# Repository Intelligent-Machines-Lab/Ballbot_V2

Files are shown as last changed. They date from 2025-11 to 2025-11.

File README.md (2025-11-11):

# Ballbot_LMI_V2

**Author:** Leandro Ventricci  
**Advisor:** Prof. Dr. Cairo Lúcio Nascimento Júnior

This repository contains the source code, STL files, and experimental results developed during research on the Ballbot platform as part of the Master of Science program in Systems and Control at the Instituto Tecnológico de Aeronáutica (ITA). The work represents a second iteration and expansion of the initial Ballbot project proposed in the master’s thesis available at [Ballbot_LMI_V1](https://github.com/pedrophj/ballbot_LMI/tree/main).

## Repository Structure

| Directory | Description |
|---|---|
| [**`/Experimental Results/Data Bags`**](./Experimental%20Results/Data%20Bags/) | Provides the ROS bag files acquired during the experiments, which contain the recorded ROS topic data used for analysis. |
| [**`/Experimental Results/Videos`**](./Experimental%20Results/Videos/) | Provides video recordings of the experimental results obtained with the Ballbot prototype. The videos are also available online at [Google Drive](https://drive.google.com/drive/folders/1ocQBuRk292TQQt81lqkflchQvDIo9T61?usp=sharing). |
| [**`/Microcontroller`**](/Microcontroller/src) | Provides the PlatformIO project containing the ESP32 firmware. |
| [**`/STL`**](/STL/) | Provides the STL files for the mechanical structure of the Ballbot for 3D printing. |
| [**`/Simulations/2D`**](/Simulations/2D) | Provides the MATLAB simulations for the X–Z and X–Y planar models, used for control design and validation. |
| [**`/Simulations/3D`**](/Simulations/3D) | Provides the CoppeliaSim files of the environment developed to validate the 2D model using a full 3D representation of the Ballbot. |

## MATLAB Simulations

The MATLAB simulation files for the Ballbot’s dynamic modeling and control are available in the [**`/Simulations/2D`**](/Simulations/2D) directory.  
These simulations cover both the X–Z and X–Y planar models, developed using **MATLAB version 2023b**.

## 3D Simulation Environment

The 3D simulation files are available in the [**`/Simulations/3D`**](/Simulations/3D) directory. The environment was developed using **CoppeliaSim Edu version 4.10**.

## Bill of Materials

The tables below list the electronic and structural components required to assemble and operate the Ballbot prototype, including specifications, quantities, and supply sources when applicable.

### Electronics

| Component | Model / Specification | Quantity |
|---|---|:---:|
| Microcontroller | ESP32-WROOM-32 | 1 |
| Microcomputer | Raspberry Pi 4 Model B (4GB) | 1 |
| Stepper Motors | NEMA 17 (17HS4401) | 3 |
| Motor Drivers | DRV8825 | 3 |
| IMU | Witmotion WT901C | 1 |
| LiDAR Sensor | RPLIDAR A2M8 | 1 |

### Structure Parts

| Part | Quantity |
|---|:---:|
| Layer 0 | 1 |
| Layer 1 | 1 |
| Layer 2 | 1 |
| Layer 3 | 1 |
| Motor Support - Layer 0 Side | 3 |
| Motor Support - Motor Side | 3 |
| Support - Layer 1 | 3 |
| Support - Layer 2 | 3 |
| Support - Layer 3 | 3 |
| Support for Electronics - Layer 1 | 1 |
| Battery Support - BMS | 1 |
| Battery Support - Connectors | 1 |
| Wheel Assembly | 3 |

### Wheel Assembly

| Part | Quantity | Notes |
|---|:---:|:---:|
| Fork | 6 | - |
| Roller - Small | 6 | - |
| Roller - Big | 6 | - |
| Motor Coupling | 1 | - |
| Motor Coupling Cap | 1 | - |
| MR52ZZ Spherical Bearing | 24 | Available at: [Aliexpress](https://pt.aliexpress.com/item/32492575669.html) |

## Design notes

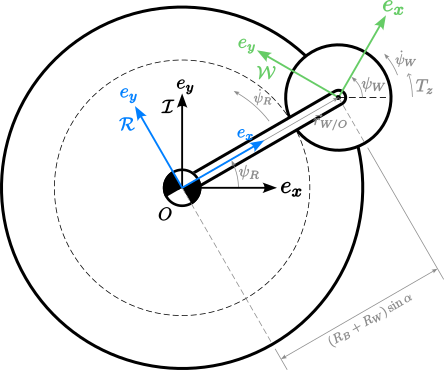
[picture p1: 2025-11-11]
Simulations/2D/XY/XY.png

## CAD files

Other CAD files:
STL/Body Structure/Support for Electronics - Layer 1.STL
STL/Wheel/Roller - Big.STL
STL/Body Structure/Motor Support - Layer 0 Side.STL
STL/Wheel/Roller - Small.STL
STL/Body Structure/Support - Layer 3.STL
STL/Wheel/Motor Coupling Cap.STL
STL/Body Structure/Layer 0.STL
STL/Wheel/Motor Coupling.STL
STL/Body Structure/Layer 2.STL
STL/Wheel/Fork.STL
STL/Body Structure/Support - Layer 1.STL
STL/Body Structure/Battery Support - BMS.STL
STL/Body Structure/Layer 3.STL
STL/Body Structure/Battery Support - Connector.STL
STL/Body Structure/Motor Support - Motor Side.STL
STL/Body Structure/Support - Layer 2.STL
STL/Body Structure/Layer 1.STL

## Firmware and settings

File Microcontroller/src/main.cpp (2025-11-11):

#include "wit_c_sdk.h"
#include "reg.h"
#include <BasicLinearAlgebra.h>
#include <Arduino.h>
#include <ArduinoOTA.h>
#include <AccelStepper.h>
#include <PID_v1_bc.h>
#include <WiFi.h>
   
#define LED_OB        2
#define RX            16
#define TX            17
#define ACC_UPDATE		0x01
#define GYRO_UPDATE		0x02
#define ANGLE_UPDATE	0x04
#define MAG_UPDATE		0x08
#define READ_UPDATE		0x80
#define g             9.81

#define MS1   33
#define MS2   14
#define MS3   32

#define MOTOR_1_STEP 12
#define MOTOR_1_DIR 13

#define MOTOR_2_STEP 19
#define MOTOR_2_DIR 18

#define MOTOR_3_STEP 25
#define MOTOR_3_DIR 26

using namespace BLA;

Matrix<3> gravity_world = {0, 0, g};
Matrix<4> pos_world, pos_robot;
Matrix<3> vel_world_out, vel_robot_out;   // Velocity data comming from sensors other than the IMU (not directly connected to the ESP32)
Matrix<3> vel_world_odom, vel_robot_odom; // Velocity data from wheels velocity
Matrix<4> vel_world, vel_world_imu, vel_robot, vel_robot_imu;
Matrix<4, 4> R_yaw;

struct FilterState {
  float filteredValue;
  bool firstRun;
}; 
FilterState gyroXFilter, gyroYFilter, gyroZFilter, 
            accXFilter, accYFilter, accZFilter,
            txFilter, tyFilter;

float lowPassFilter(float rawValue, float alpha, FilterState* state);
float alphaAccel = 1.0, alphaGyro = 0.75, alphaTorque = 1.0;

bool debug = false;
int calibDuration = 0;
int loopCount = 0, outerLoopCount = 0, integralXCount = 0, integralYCount = 0;

unsigned long timeStart;
int status = 0;

float controlRate = 200;                    // Loop Frequency in Hz
float sampleTime = 1/controlRate;           // Loop Period in s
float sat, satAngle, W1 = 0.0, W2 = 0.0, W3 = 0.0, wx = 0.0, wy = 0.0, wz = 0.0;
double satXY = 5*2*PI;
int controller = 0;

int stepRes = 32;
int stepsPerRev = 200*stepRes;

float accX_world = 0.0, accY_world = 0.0, accZ_world = 0.0, accX_robot = 0.0, accY_robot = 0.0, accZ_robot = 0.0;
float posX_world = 0.0, posY_world = 0.0, posX_world_out = 0.0, posY_world_out = 0.0, posX_world_imu = 0.0, posY_world_imu = 0.0;
float velX_world = 0.0, velY_world = 0.0;
float velX_world_imu = 0.0, velY_world_imu = 0.0;
float velX_robot_out = 0.0, velY_robot_out = 0.0, velX_world_out = 0.0, velY_world_out = 0.0;
float posXRefWorld = 0.0, posYRefWorld = 0.0, velXRefWorld = 0.0, velYRefWorld = 0.0;
float integralErroPosX = 0.0, integralErroPosY = 0.0, erroPosXAnt = 0.0, erroPosYAnt = 0.0;
float satErroPos = 0.30, satErroVel = 1.0;
float pitchMax = 1.0, rollMax = 1.0;

bool posXUpdate, posYUpdate;

struct Quaternion {
  float w, x, y, z;
};

Quaternion conjugate(Quaternion q);
Quaternion multiply(Quaternion q_1, Quaternion q_2);
Quaternion yawToQuaternion(float yaw);

float quaternionToYaw(Quaternion q);

// ------------------------------ Define the State and Controller parameters ------------------------------
struct State {
  double posX = 0.0;      // x position   [m]
  double velX = 0.0;      // x velocity   [m/s]
  double theta = 0.0;     // pitch angle  [rad]
  double q = 0.0;         // pitch rate   [rad/s]
  double posY = 0.0;      // y position   [m]
  double velY = 0.0;      // y velocity   [m/s]
  double phi = 0.0;       // roll angle   [rad]
  double p = 0.0;         // roll rate    [rad/s]
  double psi = 0.0;       // yaw angle    [rad]
  double r = 0.0;         // yaw rate     [rad/s]
};
State x, xRef;

double yawError = 0, yawErrorRef = 0;
double refTheta = 0.0, refPhi = 0.0;
double rollOffset = 0.0, pitchOffset = 0.0;
double tx = 0.0, ty = 0.0, tz = 0.0, rateTx = 0.0, rateTy = 0.0, rateTz = 0.0;
double k1 = -35.0/100.0, k2 = -110.0/100.0, k3 = 280.0/100.0, k4 = 40.0/100.0;      // Tune these values as necessary
double kp = 165.0/100.0, ki = 1.0/100.0, kd = 13.0/100.0;                         
double arKp = 0.0, arKi = 0.0, arKd = 0.0;
double posKp = 5.0/100.0, posKi = 0.0, posKd = 0.05/100.0;                      
double velKp = 10.0/100.0, velKi = 0.0, velKd = 0.5/100.0;                      
double kpYaw = 4.0/100.0, kiYaw = 0.0, kdYaw = 1.25/100;
// ---------------------------------------------------------------------------------------

// ------------------- IMU Functions and Variables -------------------
static volatile char s_cDataUpdate = 0, s_cCmd = 0xff; 
static void AutoScanSensor(void);
static void SensorUartSend(uint8_t *p_data, uint32_t uiSize);
static void SensorDataUpdata(uint32_t uiReg, uint32_t uiRegNum);
static void Delayms(uint16_t ucMs);
float fAcc[3], fGyro[3], fAngle[3];
// -------------------------------------------------------------------

//  ------------ Define PID controllers for roll and pitch ------------
PID rollPID(&x.phi, &tx, &xRef.phi, kp, ki, kd, DIRECT);
PID pitchPID(&x.theta, &ty, &xRef.theta, kp, ki, kd, DIRECT);
// PID yawPID(&x.psi, &tz, &xRef.psi, kpYaw, kiYaw, kdYaw, DIRECT);
PID yawPID(&yawError, &tz, &yawErrorRef, kpYaw, kiYaw, kdYaw, REVERSE);

PID rollRatePID(&x.p, &rateTx, &xRef.p, arKp, arKi, arKd, DIRECT);
PID pitchRatePID(&x.q, &rateTy, &xRef.q, arKp, arKi, arKd, DIRECT);
// PID yawRatePID();

PID posXPID(&x.posX, &xRef.velX, &xRef.posX, posKp, posKi, posKd, DIRECT);    // ty acts on X position -> Visualize 2D Model 
PID posYPID(&x.posY, &xRef.velY, &xRef.posY, posKp, posKi, posKd, DIRECT);    // tx acts on Y position 

PID velXPID(&x.velX, &refTheta, &xRef.velX, velKp, velKi, velKd, DIRECT);
PID velYPID(&x.velY, &refPhi, &xRef.velY, velKp, velKi, velKd, REVERSE);
// --------------------------------------------------------------------

// ------------------- Step Motor Objects -------------------
AccelStepper stepper1(1, MOTOR_1_STEP, MOTOR_1_DIR);
AccelStepper stepper2(1, MOTOR_2_STEP, MOTOR_2_DIR);
AccelStepper stepper3(1, MOTOR_3_STEP, MOTOR_3_DIR);
// ----------------------------------------------------------

// -------------- ESP32 to Raspberry Coms --------------
const uint8_t START_BYTE = 0xAA;
const uint8_t END_BYTE = 0xFF;

struct DataPacket {
    float fAngle[3];    // Angles of Attitude (Roll Pitch Yaw)
    float fGyro[3];     // Angular Velocity -> Robot Frame
    float fAcc[3];      // Linear Acceleration -> Robot "Leveled" Frame
    float vel[2];       // Linear Velocity -> Robot "Leveled" Frame
    float pos[2];       // Position -> World Frame
    float W[3];         // Angular Velocities of the planar wheels (2D Model Wheel)
};

DataPacket data;
void sendData(DataPacket data);
// -----------------------------------------------------

TaskHandle_t C0;
void loop2(void *pvParameters);
double saturate(double V, double sat);

const char* ssid = "$$$$"; // Replace with your SSID for the wifi network for OTA (Over the Air) code upload, if needed
const char* password = "$$$$"; // Replace with the password for the wifi network
bool wifiEnabled;
unsigned long wifiStartTime = 0;
const unsigned long wifiTimeout = 300000; // Wifi Timeout in milliseconds (5 minutes)

void disableWiFi();
void enableWiFiAndOTA();
void blinkLED(int times);
void velocityConversion();
Matrix<3, 3> rotationMatrix(const int& axis, const float& angle);
Matrix<4, 4> transformMatrix(const float& angle, Matrix<4> position);
Matrix<3, 3> robotToWorldRotation(const Matrix<3>& angles);

// ------------------ LQR Controller ------------------
class LQR {
  private:
    double k1, k2, k3, k4;

  public:
    // Constructor to initialize LQR gains
    LQR(double k1, double k2, double k3, double k4) {
      this->k1 = k1;
      this->k2 = k2;
      this->k3 = k3;
      this->k4 = k4;
    }

    void setGains(double k1, double k2, double k3, double k4) {
      this->k1 = k1;
      this->k2 = k2;
      this->k3 = k3;
      this->k4 = k4;
    }

    // Update function to calculate control inputs
    // State Vector x -> [x, x_dot, theta, theta_dot, y, y_dot, phi, phi_dot]
    void update(State xRef, State x, double &tx, double &ty) {
      // Calculate the error for each variable
      double erroPosX = xRef.posX - x.posX;
      double erroVelX = xRef.velX - x.velX;
      double erroTheta = xRef.theta - x.theta;
      double erroq = xRef.q - x.q;

      double erroPosY = xRef.posY - x.posY;
      double erroVelY = xRef.velY - x.velY;
      double erroPhi = xRef.phi - x.phi;
      double errop = xRef.p - x.p;

      // Anti-windup for X and Y position controllers
      // When the counter is active (greater than 0), the corresponding integrator value 
      // is gradually reduced at each iteration to prevent saturation.
      if ((erroPosXAnt < 0 && erroPosX > 0) || (erroPosXAnt > 0 && erroPosX < 0))
      {
          integralXCount = 200;
      }

      if ((erroPosYAnt < 0 && erroPosY > 0) || (erroPosYAnt > 0 && erroPosY < 0))
      {
          integralYCount = 200;
      }
      
      if (integralXCount > 0)
      {
          integralXCount--;
          integralErroPosX *= 0.98;
      }

      if (integralYCount > 0)
      {
          integralYCount--;
          integralErroPosY *= 0.98;
      }

      erroPosXAnt = erroPosX;
      erroPosYAnt = erroPosY;

      // This tries to compensate for the mass unbalance on the x-z plane (we have only one motor at the front of the robot and two at the rear)
      if (erroPosX > satErroPos*1.2) erroPosX = satErroPos*1.2;
      if (erroPosX < -satErroPos) erroPosX = -satErroPos;
      // erroPosX = saturate(erroPosX, satErroPos);
      erroPosY = saturate(erroPosY, satErroPos*1.25);

      integralErroPosX += erroPosX*sampleTime;
      integralErroPosY += erroPosY*sampleTime;

      integralErroPosX = saturate(integralErroPosX, 1.25*satErroPos);
      integralErroPosY = saturate(integralErroPosY, 1.25*satErroPos);
      
      float absErroX = fabs(erroPosX);
      float absErroY = fabs(erroPosY);

      tx = -(integralErroPosY*ki) + (erroPosY * k1) + (erroVelY * k2) + (erroPhi * k3) + (errop * k4);    
      ty = (integralErroPosX*ki) - (erroPosX * k1) - (erroVelX * k2) + (erroTheta * k3) + (erroq * k4);
    }
};

LQR lqrController(k1, k2, k3, k4);
// ----------------------------------------------------

#pragma pack(push, 1)
struct CommandPacket {
    uint8_t start_byte;
    uint8_t cmd_type;
    float cmd_value;
    uint8_t end_byte;
};
#pragma pack(pop)

enum CommandType {
    CMD_CONTROLLER_SELECT = 0,
    CMD_KP,
    CMD_KI,
    CMD_KD,
    CMD_KP_ANGLE_RATE,
    CMD_KI_ANGLE_RATE,
    CMD_KD_ANGLE_RATE,
    CMD_KP_POS,
    CMD_KI_POS,
    CMD_KD_POS,
    CMD_KP_VEL,
    CMD_KI_VEL,
    CMD_KD_VEL,
    CMD_K1,
    CMD_K2,
    CMD_K3,
    CMD_K4,
    CMD_KP_YAW,
    CMD_KI_YAW,
    CMD_KD_YAW,
    CMD_SATURATION,
    CMD_POS_X,
    CMD_POS_Y,
    CMD_VEL_X,
    CMD_VEL_Y,
    CMD_YAW,
    CMD_POS_X_SETPOINT,
    CMD_POS_Y_SETPOINT,
    CMD_VEL_X_SETPOINT,
    CMD_VEL_Y_SETPOINT,
    CMD_ROLL_SETPOINT,
    CMD_PITCH_SETPOINT,
    CMD_YAW_SETPOINT,
    CMD_ACCEL_FILTER,
    CMD_GYRO_FILTER,
    CMD_TORQUE_FILTER,
    CMD_SAT_ERRO_POS,
    CMD_SAT_ERRO_VEL,
    CMD_ROLL_MAX,
    CMD_PITCH_MAX,
    CMD_WIFI_MODE,
    CMD_ACCEL_CALIB,
    CMD_DEBUG,
    CMD_MICRO_STEP,
    NUM_COMMANDS
};
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
void loop() {
  for(;;) {
    /*
      Motor angular velocity unit is -> Wn [rad/s]
      setSpeed input is [steps/s]
      We must convert from [rad/s] to [steps/s]
      As we are using micro-stepping, one revolution (2pi) has 6400 steps. (e.g. microstepping set to 32, then 200*32)
      We have to multiply V by 6400/2pi [steps/rad].
      1/(2pi) = 0.15915
    */   
    if (controller == -1) {
      stepper1.setSpeed(stepsPerRev * 0.15915 * k1);
      stepper2.setSpeed(stepsPerRev * 0.15915 * k2);
      stepper3.setSpeed(stepsPerRev * 0.15915 * k3);
    }

    else {
      stepper1.setSpeed(stepsPerRev * 0.15915 * W1);
      stepper2.setSpeed(stepsPerRev * 0.15915 * W2);
      stepper3.setSpeed(stepsPerRev * 0.15915 * W3);
    }

    // Run motors
    stepper1.runSpeed();
    stepper2.runSpeed();
    stepper3.runSpeed();
  }
}

void loop2( void *pvParameters ) {
  for(;;) {     
    timeStart = micros(); 

    cmdHandler.processSerial();

    // Handle OTA updates if Wi-Fi is enabled
    if (wifiEnabled) {
      ArduinoOTA.handle();

      // Automatically disable Wi-Fi after a timeout
      if (millis() - wifiStartTime > wifiTimeout) {
        disableWiFi();
      }
    }

    while (Serial1.available())
    {
      WitSerialDataIn(Serial1.read());
    }

    if(s_cDataUpdate)
    {
      for(int i = 0; i < 3; i++)
      {
        fAcc[i] = sReg[AX+i] / 32768.0f * 16.0f;
        fGyro[i] = sReg[GX+i] / 32768.0f * 2000.0f;
        fAngle[i] = sReg[Roll+i] / 32768.0f * 180.0f;
      }
      
      if(s_cDataUpdate & ACC_UPDATE); s_cDataUpdate &= ~ACC_UPDATE;		
      if(s_cDataUpdate & GYRO_UPDATE); s_cDataUpdate &= ~GYRO_UPDATE;
      if(s_cDataUpdate & ANGLE_UPDATE); s_cDataUpdate &= ~ANGLE_UPDATE;			
      if(s_cDataUpdate & MAG_UPDATE); s_cDataUpdate &= ~MAG_UPDATE;
      
      s_cDataUpdate = 0;
    }

    x.phi = fAngle[0]*DEG_TO_RAD;                             // [rad]
    x.theta = fAngle[1]*DEG_TO_RAD;                           // [rad]
    // x.psi = fAngle[2]*DEG_TO_RAD;                          // [rad] Yaw info is comming from Outside 
    
    x.p = fGyro[0]*DEG_TO_RAD;                                // [rad/s]
    x.q = fGyro[1]*DEG_TO_RAD;                                // [rad/s]
    x.r = fGyro[2]*DEG_TO_RAD;                                // [rad/s]
   
    x.p = lowPassFilter(x.p, alphaGyro, &gyroXFilter);
    x.q = lowPassFilter(x.q, alphaGyro, &gyroYFilter);
    x.r = lowPassFilter(x.r, alphaGyro, &gyroZFilter);

    Matrix<3> angles = {(float)x.phi, (float)x.theta, (float)x.psi};

    // We are transforming the Robot's acceleration from body frame to inertial frame
    Matrix<3> acc_robot = {(float)(fAcc[0]*g), (float)(fAcc[1]*g), (float)(fAcc[2]*g)};  // [m/s^2]
    Matrix<3, 3> R_robot_to_world = robotToWorldRotation(angles);
    Matrix<3> acc_world = (R_robot_to_world*acc_robot) - gravity_world;

    accX_world = lowPassFilter(acc_world(0), alphaAccel, &accXFilter);
    accY_world = lowPassFilter(acc_world(1), alphaAccel, &accYFilter);
    accZ_world = lowPassFilter(acc_world(2), alphaAccel, &accZFilter);
    
    vel_robot_odom = {float (-wy*0.07/2), float (wx*0.07/2), 0};
    vel_world_odom = robotToWorldRotation(Matrix<3> {0, 0, (float) x.psi})*vel_robot_odom;

    velX_world_imu = velX_world + accX_world*sampleTime;
    velY_world_imu = velY_world + accY_world*sampleTime;
    vel_world_imu = {velX_world_imu, velY_world_imu, 0, 0};

    velX_world = 0.004*vel_world_odom(0) + 0.996*velX_world_imu;
    velY_world = 0.004*vel_world_odom(1) + 0.996*velY_world_imu;

    vel_world = {velX_world, velY_world, 0, 0};
    vel_robot = R_yaw*vel_world;
    
    x.velX = vel_robot(0); x.velY = vel_robot(1);

    posX_world_imu = posX_world + velX_world_imu*sampleTime;
    posY_world_imu = posY_world + velY_world_imu*sampleTime;

    posX_world = 0.99*posX_world_out + 0.01*posX_world_imu; 
    posY_world = 0.99*posY_world_out + 0.01*posY_world_imu;
    
    pos_world = {posX_world, posY_world, 0, 1};

    // Transforming Acceleration, Position and Velocity to the "Leveled" robot's frame, 
    // which is a frame fixed to the Robot's body and that has its X-Y plane aligned to the Inertial frame X-Y plane.
    // Note that for Position, we're also translating it to the robot's frame, which means the position should be 0 at any time, 
    // as we're measuring the robot's position related to it's own frame of reference that has it's origint at the robot's C.G
    R_yaw = transformMatrix(x.psi, pos_world);    

    pos_robot = R_yaw*pos_world;
    x.posX = pos_robot(0); x.posY = pos_robot(1);

    Matrix<4> acc_robot_leveled = R_yaw * Matrix<4> {acc_world(0), acc_world(1), acc_world(2), 0};
    accX_robot = acc_robot_leveled(0); accY_robot = acc_robot_leveled(1); accZ_robot = acc_robot_leveled(2); 

    Matrix<4> pos_ref_world = {posXRefWorld, posYRefWorld, 0, 1};
    Matrix<4> pos_ref_robot = R_yaw * pos_ref_world;
    xRef.posX = pos_ref_robot(0); xRef.posY = pos_ref_robot(1);    

    Quaternion qSP = yawToQuaternion(xRef.psi);
    Quaternion qCur = yawToQuaternion(x.psi);
    Quaternion qDelta = multiply(qSP, conjugate(qCur));

    yawError = quaternionToYaw(qDelta);
    if ((yawError*RAD_TO_DEG) > 15){
      yawError = 15*DEG_TO_RAD;
    }

    if ((yawError*RAD_TO_DEG) < -15){
      yawError = -15*DEG_TO_RAD;
    }
    
    if (controller == 0)
    {
      // Roll Pitch Yaw
      rollPID.SetSampleTime((int)(sampleTime*1000));      // Input is [ms], converting from [s] to [ms]
      pitchPID.SetSampleTime((int)(sampleTime*1000));     
      yawPID.SetSampleTime((int)(sampleTime*1000));

      rollRatePID.SetSampleTime((int)(sampleTime*100));
      pitchRatePID.SetSampleTime((int)(sampleTime*100));

      xRef.phi = rollOffset;
      xRef.theta = pitchOffset;

      rollPID.Compute();
      pitchPID.Compute();
      yawPID.Compute();

      rollRatePID.Compute();
      pitchRatePID.Compute();

      tx = lowPassFilter(tx, alphaTorque, &txFilter);
      ty = lowPassFilter(ty, alphaTorque, &tyFilter);

      wx += tx + rateTx; //*47619.047*(1/controlRate);         // This is 2D Wheel x Angular Velocity
      wy += ty + rateTy; //*47619.047*(1/controlRate);         // This is 2D Wheel Y Angular Velocity
      wz += tz; //*47619.047*(1/controlRate);                  // This is 2D Wheel Z Angular Velocity

      velocityConversion();
    }

    else if (controller == 1) {
      if (outerLoopCount == 0)
      {
        // The Outer Control Loop should run at a lower frequency since position updates are received at 30 Hz
        posXPID.SetSampleTime((int)(sampleTime*1000/3));
        posYPID.SetSampleTime((int)(sampleTime*1000/3));
        
        posXPID.Compute();
        posYPID.Compute();

        xRef.velX = saturate(xRef.velX, 0.1);
        xRef.velY = saturate(xRef.velY, 0.1);

        velXPID.SetSampleTime((int)(sampleTime*1000/3));
        velYPID.SetSampleTime((int)(sampleTime*1000/3));

        velXPID.Compute();
        velYPID.Compute();
        
        refPhi = saturate(refPhi, rollMax*DEG_TO_RAD);
        refTheta = saturate(refTheta, pitchMax*DEG_TO_RAD);        
        
        xRef.phi = refPhi + rollOffset;
        xRef.theta = refTheta + pitchOffset;

        outerLoopCount++;
      }

      else {
        outerLoopCount++;
        if (outerLoopCount == 3) outerLoopCount = 0;        
      }       

      rollPID.SetSampleTime((int)(sampleTime*1000));
      pitchPID.SetSampleTime((int)(sampleTime*1000));     
      yawPID.SetSampleTime((int)(sampleTime*1000));

      rollPID.Compute();
      pitchPID.Compute();
      yawPID.Compute();

      rollRatePID.Compute();
      pitchRatePID.Compute();

      tx = lowPassFilter(tx, alphaTorque, &txFilter);
      ty = lowPassFilter(ty, alphaTorque, &tyFilter);

      wx += tx + rateTx; //*47619.047*(1/controlRate);         // This is 2D Wheel x Angular Velocity
      wy += ty + rateTy; //*47619.047*(1/controlRate);         // This is 2D Wheel Y Angular Velocity
      wz += tz; //*47619.047*(1/controlRate);                  // This is 2D Wheel Z Angular Velocity

      velocityConversion();
    }

    else if (controller == 2)
    {
      Matrix<4> vel_ref_world = {velXRefWorld, velYRefWorld, 0, 0};
      Matrix<4> vel_ref_robot = R_yaw * vel_ref_world;
      xRef.velX = vel_ref_robot(0); xRef.velY = vel_ref_robot(1);

      xRef.phi = rollOffset;
      xRef.theta = pitchOffset;

      lqrController.setGains(k1, k2, k3, k4);
      lqrController.update(xRef, x, tx, ty);

      tx = lowPassFilter(tx, alphaTorque, &txFilter);
      ty = lowPassFilter(ty, alphaTorque, &tyFilter);

      // xRef.psi = atan2(xRef.posY, xRef.posX);

      yawPID.SetSampleTime((int)(sampleTime*1000));
      yawPID.Compute();
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

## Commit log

2025-11-11 Initial project structure.
    Add project directories, microcontroller source code, simulation files, STL models, experimental data bags, and videos.
    [Battery Support - BMS.STL, Battery Support - Connector.STL, Fork.STL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]
2025-11-11 Update README with new directories and local links
    Added descriptions and local links for Data Bags and Videos directories. Updated simulation and STL directory links to use local paths instead of external URLs for consistency and clarity.
